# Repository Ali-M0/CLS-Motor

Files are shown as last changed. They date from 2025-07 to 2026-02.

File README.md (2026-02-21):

# CLS-Motor: A compact solution for stepper motors
<br>
<br>

Screenshot 2025-07-10 at 8 18 01 PM

<br>
<br>

          

<br>
Why not improve the capabilities of an already abundant and capable motor.
<br>

## Key Features

<br>
- Real-time closed-loop correction using MT6816 magnetic encoder
<br>
- **Communication via CAN bus:** By utilizing a CAN bus communication protocol, you inherently gain several benefits to your system, the main benefits being a robust communication protocol that was made with low EMI in mind, along with a more accurate system that decreases the amount of wires needed and scalability with other CLS-Motor systems.
<br>
- **6-layer custom PCB:** Designed in KiCad for signal integrity and thermal performance
<br>
- **Onboard STM32F103CBT6:** Handles encoder data and CAN communication
<br>
- Power regulation via LP2992AIM5-3.3 linear regulator
<br>
- Fully custom C++ to come (CLion environment)

<br>
<br>

## Motivation
In robotic systems—especially robotic arms—accuracy and reliability are critical. While working on my own robotic arm project, I noticed that traditional open-loop stepper motors often missed steps under load, compromising precision.
<br>
<br>
To solve this, I developed the Closed-Loop Stepper (CLS) Motor system—an integrated hardware/software solution that enables real-time position correction through encoder feedback and control logic.
<br>
<br>
<br>

FUTURE PLANS
<br>

># Correction Software for CLS Motor
>
><br>
><br>
>
> Explanation about my STM32 programming coming soon with demo and visuals.
> <br>
> Implementation of a diagnostic serial output to aid in tuning and debugging the control loop in real-world conditions.
> <br>
> Custom C++ software using a PID control system and FOC controller to detect missing steps, sending signals to then correct the lost steps
> <br>
>

<br>
<br>
<br>
<br>

## Technical Specifications/Overview

<br>

A closed-loop control system designed to stack with stepper motors and provide real-time feedback using a magnetic encoder. It detects missed steps and corrects them using an onboard STM32 microcontroller while also supplying your communication line through the CAN bus ports to your main microcontroller.

  <br>

In the field of robotics, precision and reliability in motor control are essential. During the development of my robotic arm project, I identified the limitations of traditional open-loop stepper systems, particularly their inability to self-correct under load. To address this, I designed and implemented a closed-loop stepper motor driver, combining custom hardware and software to enable real-time position correction.

  <br>

This project involved designing a 6-layer PCB in KiCad, optimized for signal integrity and thermal performance. At its core is an STM32F103CBT6 microcontroller, chosen for its surprisingly high processing speed, rich I/O capabilities, and the fact that its only main purpose is to power the encoder and CAN transceiver, along with any other I/O necessary within the board. I integrated an MT6816 magnetic rotary encoder on the rear shaft of a NEMA 17 stepper motor to provide high-resolution feedback, enabling the system to compare target and actual positions. Through custom correction software written in C++ using CLion, the CLS system adjusts its actuation based on the previous and current step resolution. The CLS motor system also integrates an SN65HVD232 CAN transceiver that, on the surface, enables communication between the main CAN controller located on the main MCU, that being a Teensy 4.1, and the CAN bus ports, supplying my system with its communication signal.

  <br>

You also may be wondering how my system is powered. That's done through a cascade power system that cascades through a daisy chain design and supplies power to all motors using the CLS motor system, being ultimately powered by a +5V power supply that's soldered to the PCB's positive and negative solder pads added to the top and bottom of the board. The system regulates the +5V power supply to a +3.3V output rail through an LP2992AIM5-3.3 linear regulator, and this then provides power to all the necessary components within my system.

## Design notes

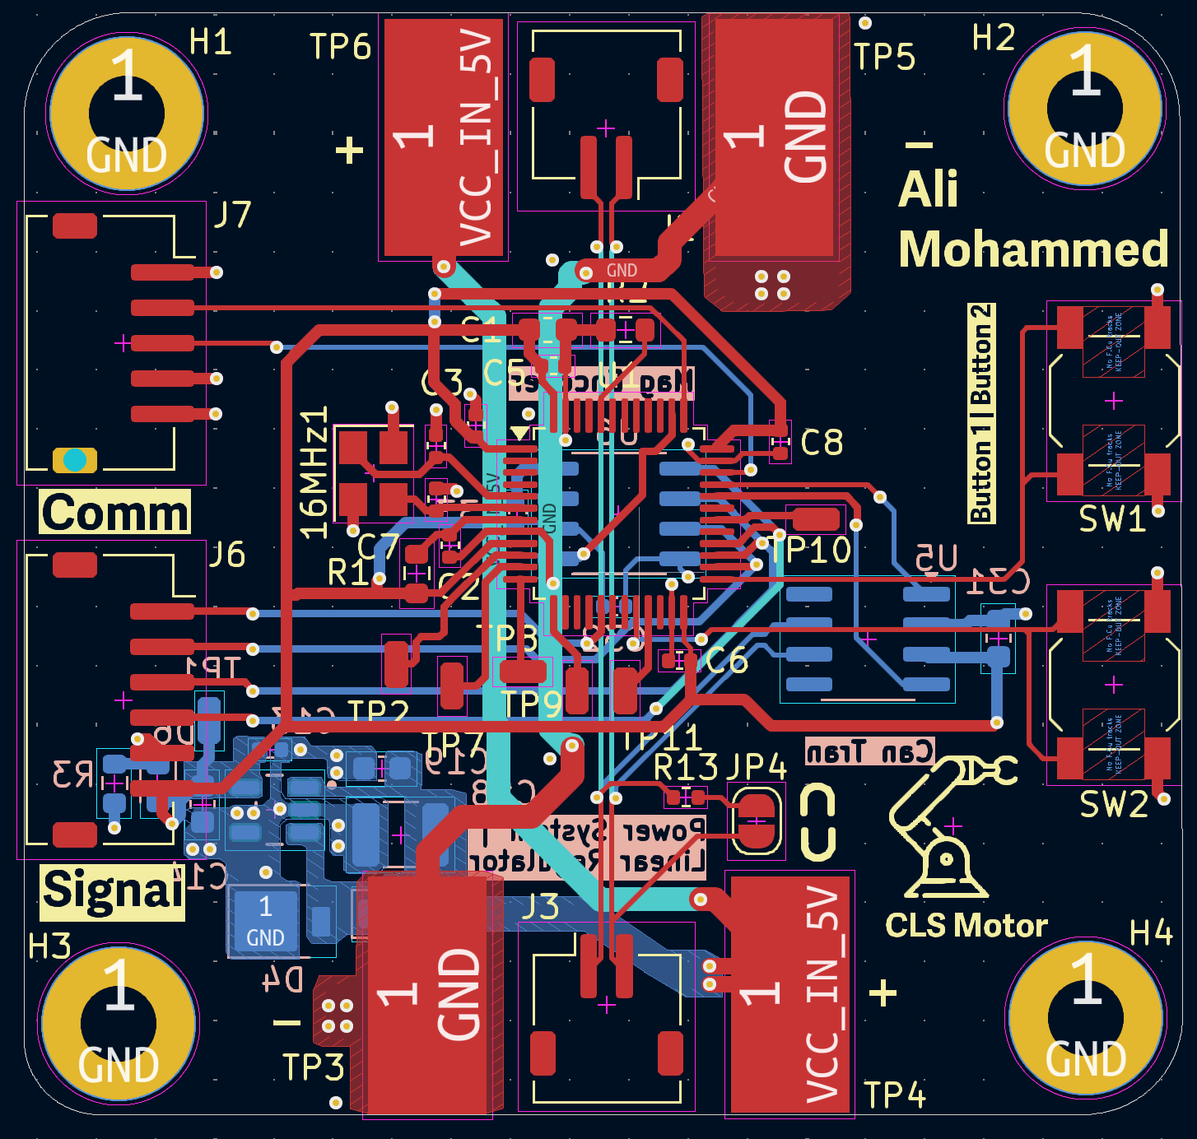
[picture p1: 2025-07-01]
Images/PCB Design in Software.png

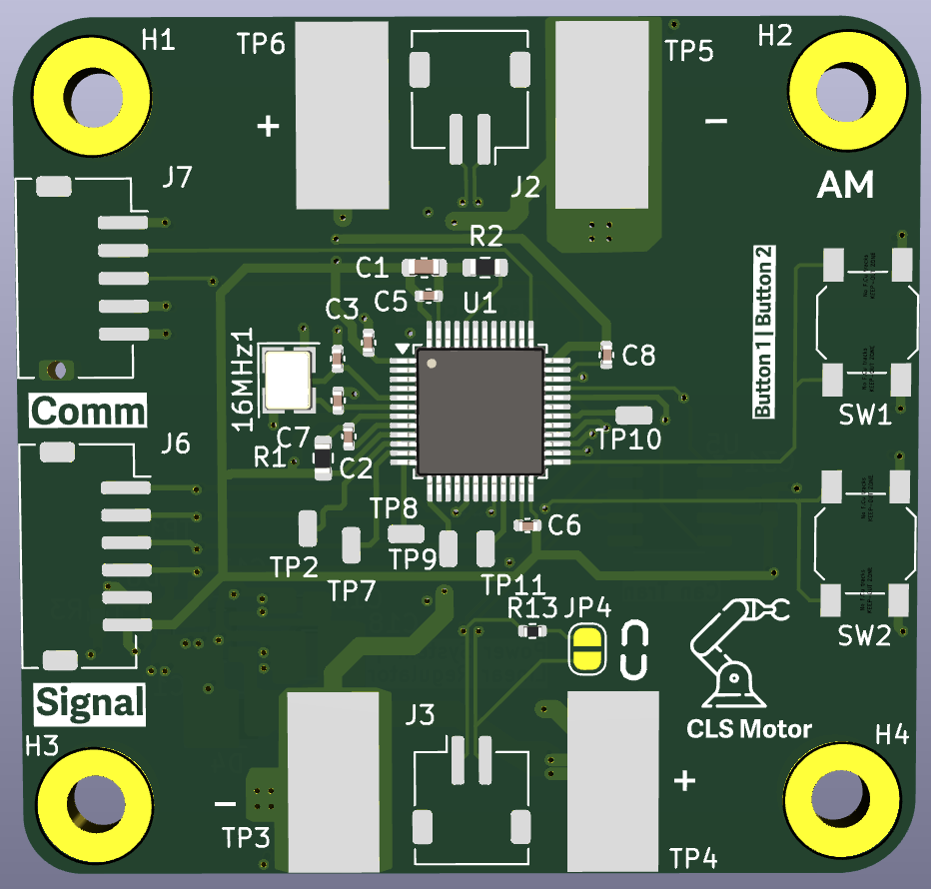
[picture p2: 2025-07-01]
Images/PCB Render (Front).png

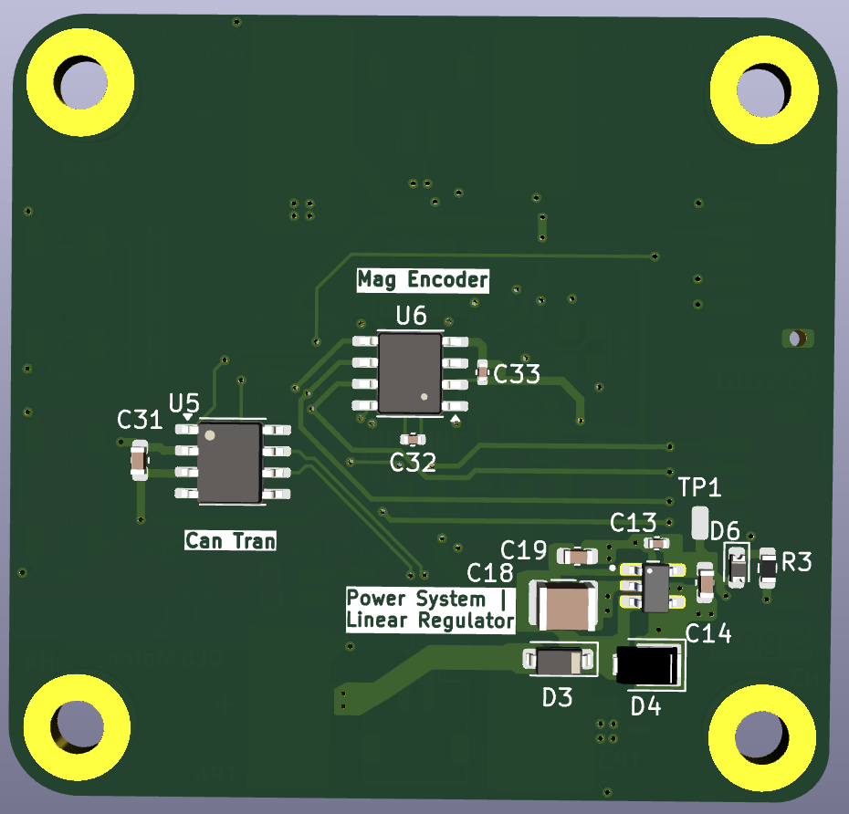
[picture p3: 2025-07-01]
Images/PCB Render (Back).png

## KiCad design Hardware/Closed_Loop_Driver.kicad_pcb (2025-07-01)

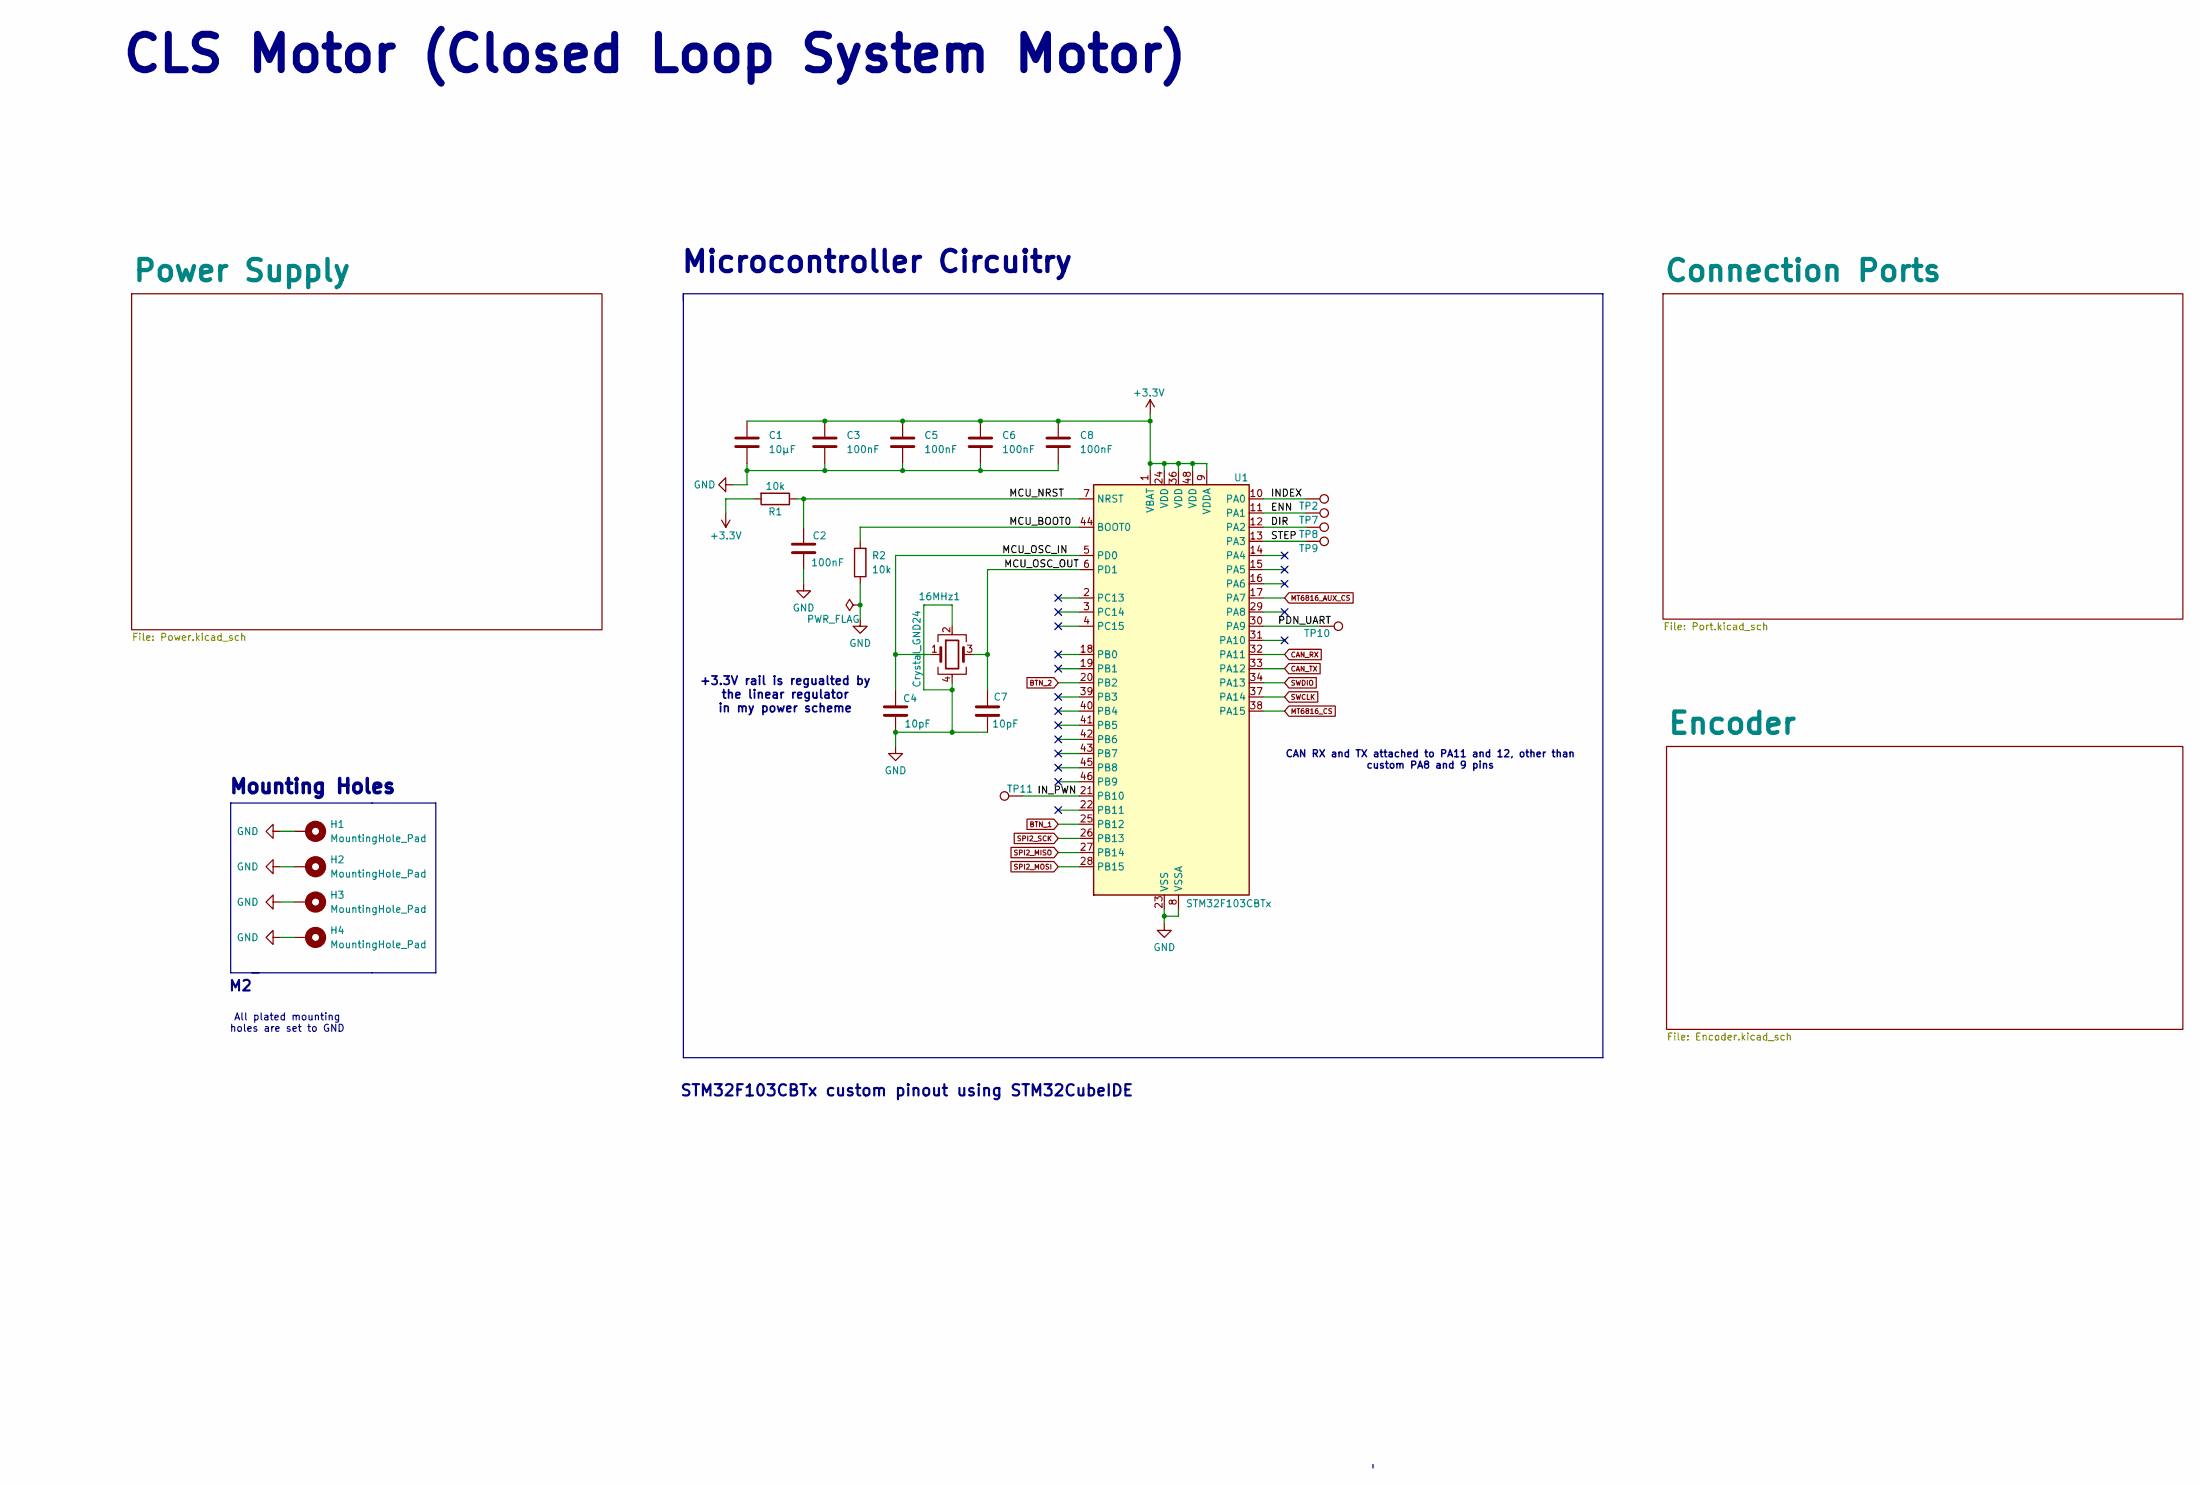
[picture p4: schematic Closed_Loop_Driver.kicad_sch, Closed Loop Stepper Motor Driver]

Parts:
16MHz1: Crystal_GND24; Crystal_SMD_3225-4Pin_3.2x2.5mm
C1: 10µF; C_0603_1608Metric
C2, C3, C5, C6, C8: 100nF; C_0402_1005Metric
C4, C7: 10pF; C_0402_1005Metric
H1, H2, H3, H4: MountingHole_Pad; MountingHole_3.2mm_M3_Pad
R1, R2: 10k; R_0603_1608Metric
TP2, TP7, TP8, TP9, TP10, TP11: TestPoint; SolderWirePad_1x01_SMD_1x2mm
U1: STM32F103CBTx; LQFP-48_7x7mm_P0.5mm

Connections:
+3.3V: C1.1, C3.1, C5.1, C6.1, C8.1, R1.2, U1.1 (VBAT), U1.9 (VDDA), U1.24 (VDD), U1.36 (VDD), U1.48 (VDD); also elsewhere on the board
/DIR: TP8.1, U1.12 (PA2)
/ENN: TP7.1, U1.11 (PA1)
/INDEX: TP2.1, U1.10 (PA0)
/IN_PWN: TP11.1, U1.21 (PB10)
/MCU_BOOT0: R2.2, U1.44 (BOOT0)
/MCU_NRST: C2.1, R1.1, U1.7 (NRST)
/MCU_OSC_IN: 16MHz1.1, C4.1, U1.5 (PD0)
/MCU_OSC_OUT: 16MHz1.3, C7.1, U1.6 (PD1)
/PDN_UART: TP10.1, U1.30 (PA9)
/STEP: TP9.1, U1.13 (PA3)
BTN_1: U1.25 (PB12); also elsewhere on the board
BTN_2: U1.20 (PB2); also elsewhere on the board
CAN_RX: U1.32 (PA11); also elsewhere on the board
CAN_TX: U1.33 (PA12); also elsewhere on the board
GND: 16MHz1.2, 16MHz1.4, C1.2, C2.2, C3.2, C4.2, C5.2, C6.2, C7.2, C8.2, H1.1, H2.1, H3.1, H4.1, R2.1, U1.8 (VSSA), U1.23 (VSS), U1.35 (VSS), U1.47 (VSS); also elsewhere on the board
MT6816_AUX_CS: U1.17 (PA7); also elsewhere on the board
MT6816_CS: U1.38 (PA15); also elsewhere on the board
SPI2_MISO: U1.27 (PB14); also elsewhere on the board
SPI2_MOSI: U1.28 (PB15); also elsewhere on the board
SPI2_SCK: U1.26 (PB13); also elsewhere on the board
SWCLK: U1.37 (PA14); also elsewhere on the board
SWDIO: U1.34 (PA13); also elsewhere on the board

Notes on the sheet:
CLS Motor (Closed Loop System Motor)
CAN RX and TX attached to PA11 and 12, other than custom PA8 and 9 pins
All plated mounting holes are set to GND
Microcontroller Circuitry
+3.3V rail is regualted by the linear regulator in my power scheme
Mounting Holes
STM32F103CBTx custom pinout using STM32CubeIDE

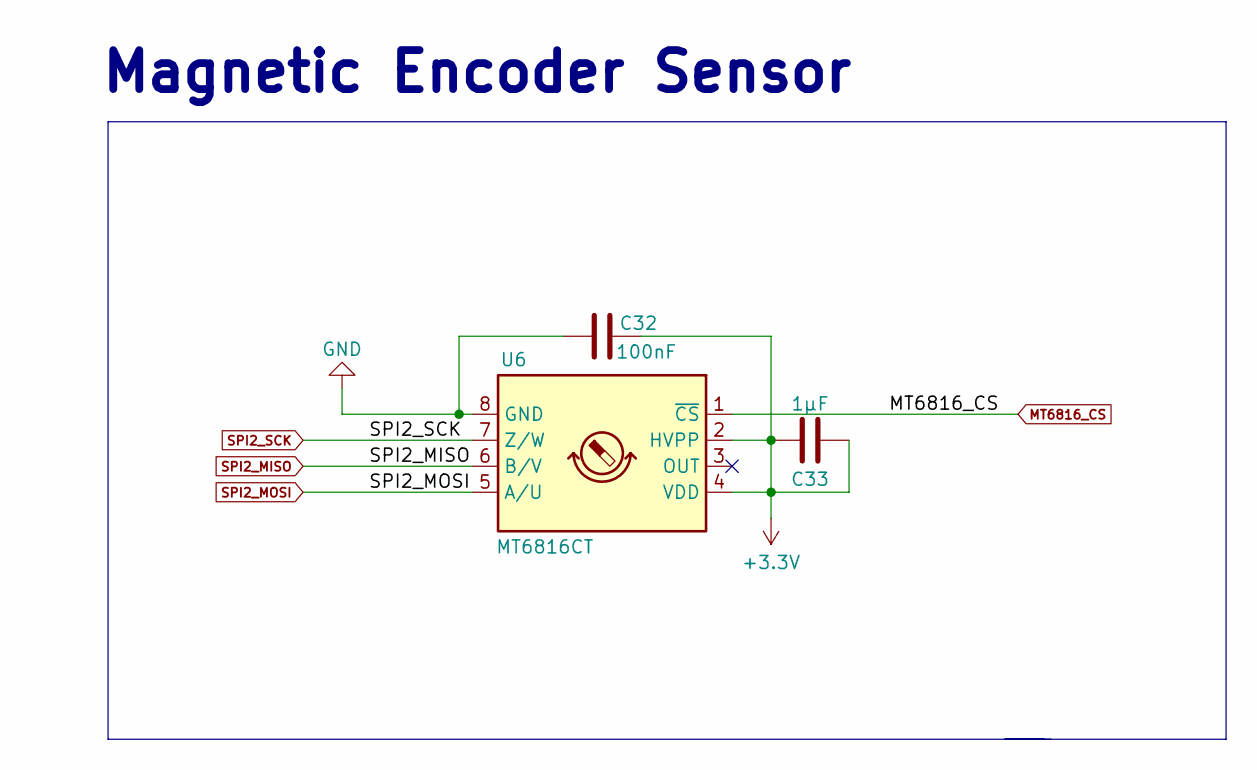
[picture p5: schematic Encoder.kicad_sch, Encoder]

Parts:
C32: 100nF; C_0402_1005Metric
C33: 1µF; C_0402_1005Metric
U6: MT6816CT; SO-8_3.9x4.9mm_P1.27mm

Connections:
+3.3V: C32.1, C33.1, C33.2, U6.2 (HVPP), U6.4 (VDD); also elsewhere on the board
GND: C32.2, U6.8 (GND); also elsewhere on the board
MT6816_CS: U6.1 (~CS); also elsewhere on the board
SPI2_MISO: U6.6 (B/V); also elsewhere on the board
SPI2_MOSI: U6.5 (A/U); also elsewhere on the board
SPI2_SCK: U6.7 (Z/W); also elsewhere on the board

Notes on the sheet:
Magnetic Encoder Sensor

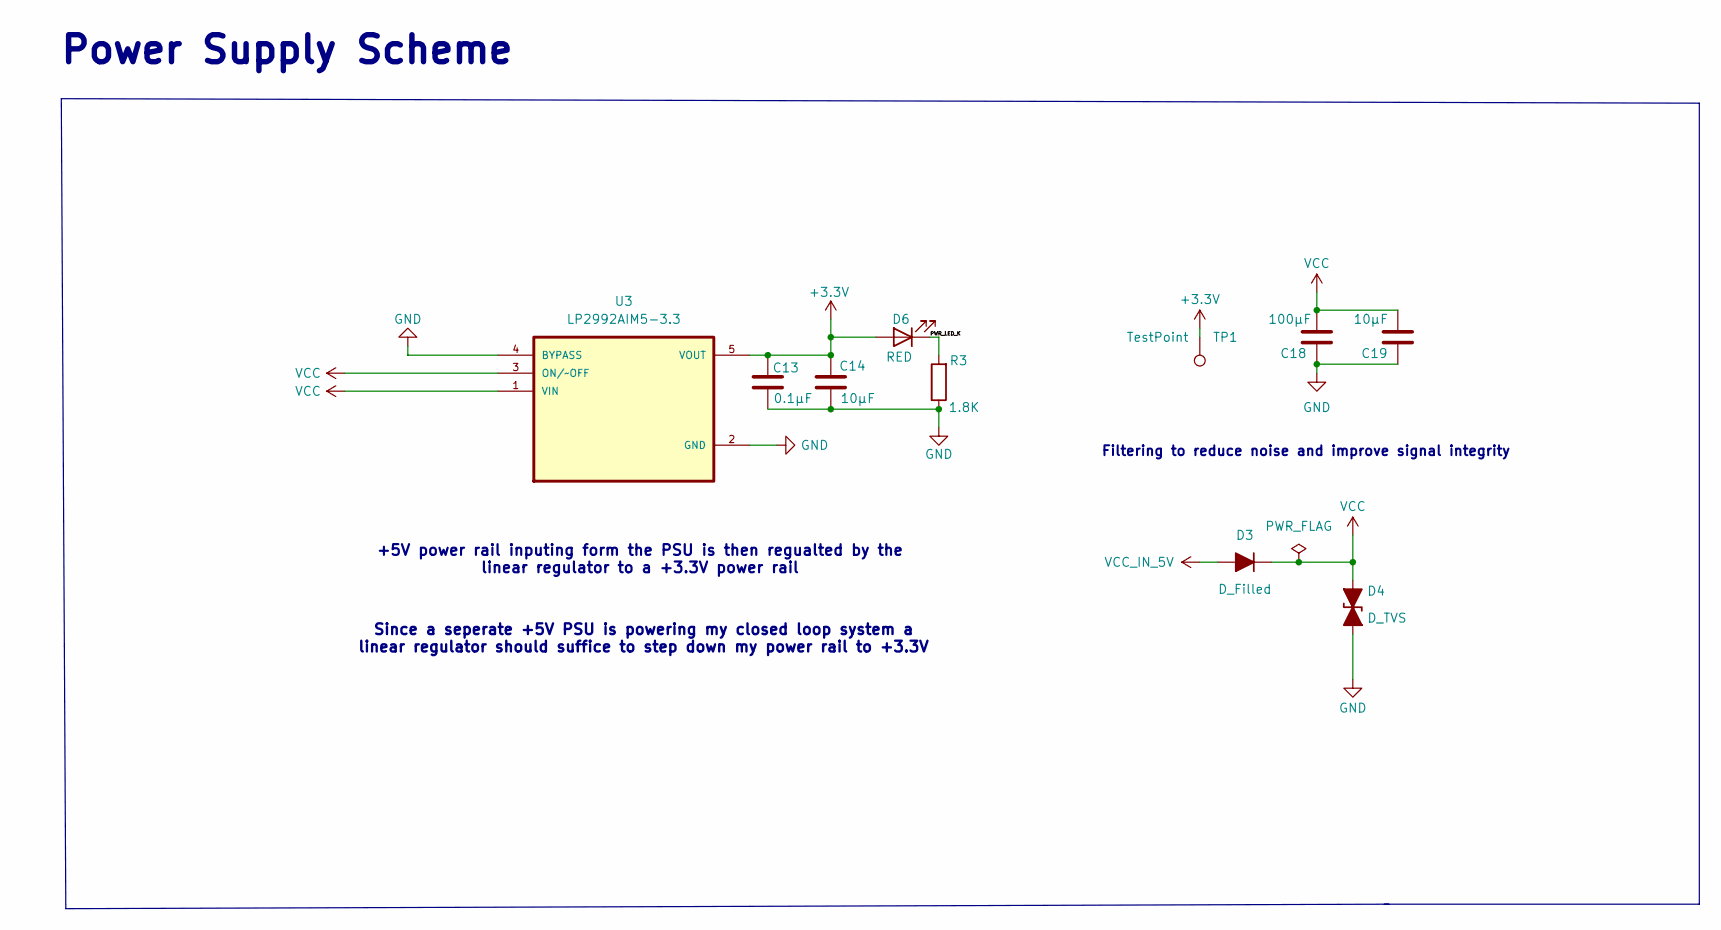
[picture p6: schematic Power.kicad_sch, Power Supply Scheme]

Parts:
C13: 0.1µF; C_0402_1005Metric
C14, C19: 10µF; C_0603_1608Metric
C18: 100µF; C_1210_3225Metric
D3: D_Filled; D_SOD-123
D4: D_TVS; D_SMP_DO-220AA
D6: RED; D_0603_1608Metric
R3: 1.8K; R_0603_1608Metric
TP1: TestPoint; SolderWirePad_1x01_SMD_1x2mm
U3: LP2992AIM5-3.3; SOT95P280X145-5N

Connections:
+3.3V: C13.1, C14.2, D6.2 (A), TP1.1, U3.5 (VOUT); also elsewhere on the board
/Power Supply/PWR_LED_K: D6.1 (K), R3.2
GND: C13.2, C14.1, C18.2, C19.2, D4.1 (A1), R3.1, U3.2 (GND), U3.4 (BYPASS); also elsewhere on the board
VCC: C18.1, C19.1, D3.1 (K), D4.2 (A2), U3.1 (VIN), U3.3 (ON/~OFF)
VCC_IN_5V: D3.2 (A); also elsewhere on the board

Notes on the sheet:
+5V power rail inputing form the PSU is then regualted by the linear regulator to a +3.3V power rail
Power Supply Scheme
Since a seperate +5V PSU is powering my closed loop system a linear regulator should suffice to step down my power rail to +3.3V
Filtering to reduce noise and improve signal integrity

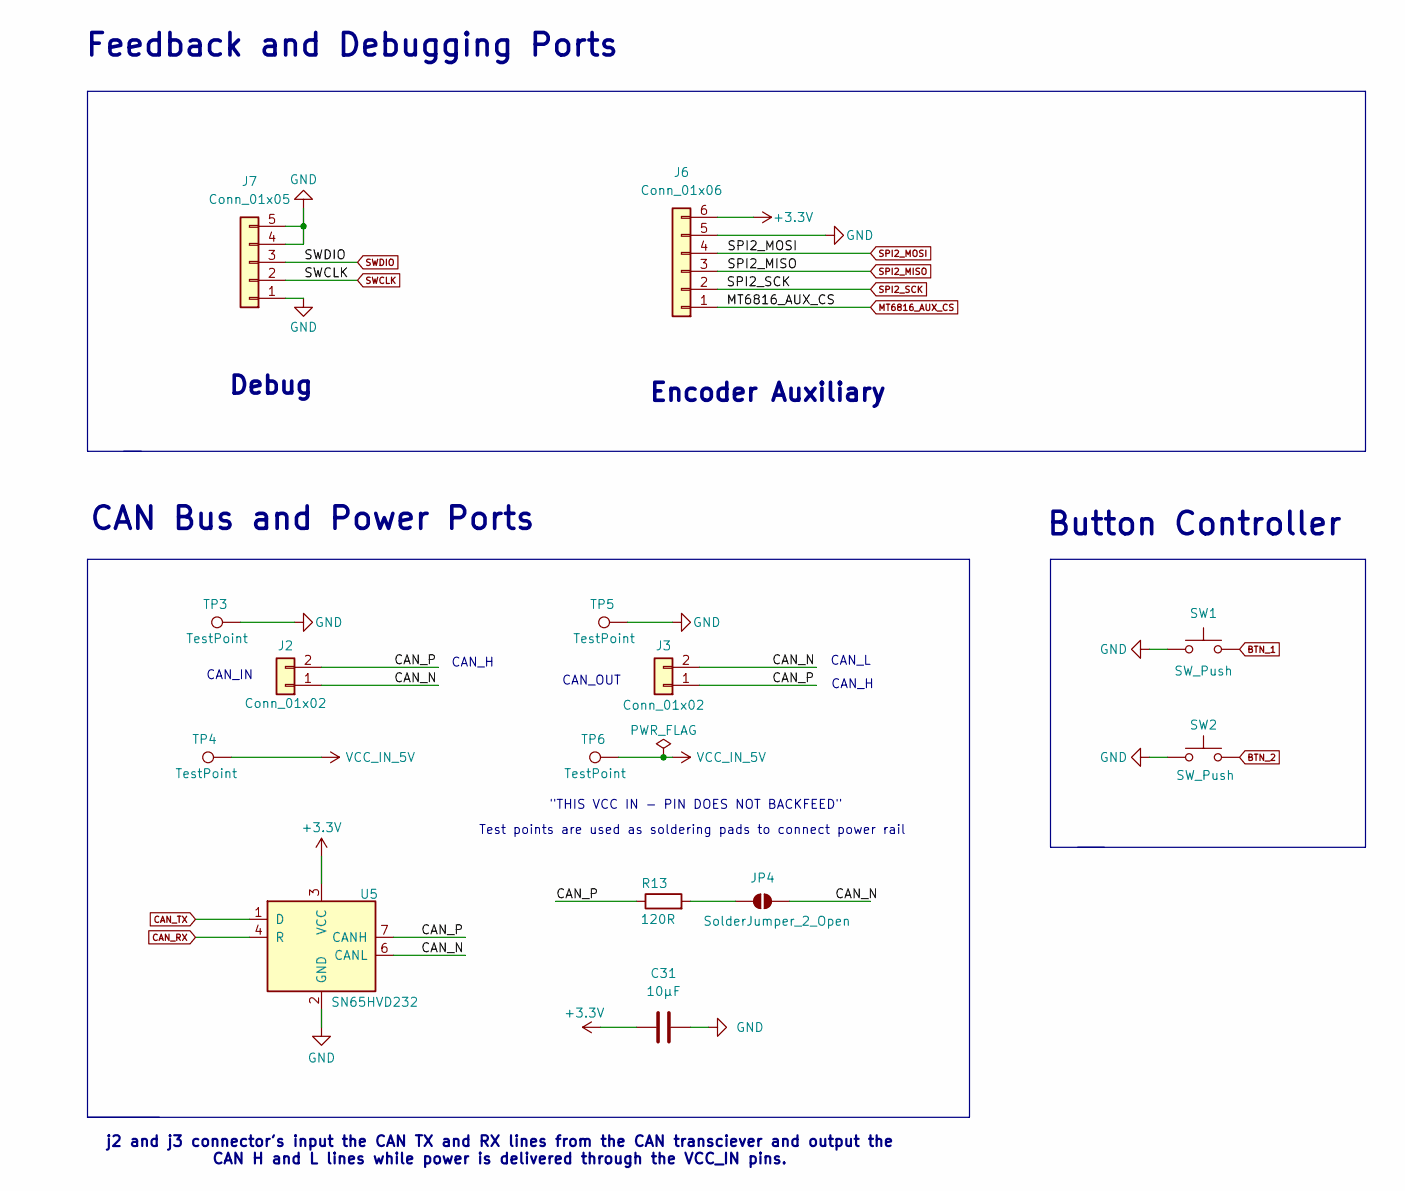
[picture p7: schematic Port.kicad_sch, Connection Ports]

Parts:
C31: 10µF; C_0603_1608Metric
J2, J3: Conn_01x02; JST_ZH_S2B-ZR-SM4A-TF_1x02-1MP_P1.50mm_Horizontal
J6: Conn_01x06; JST_ZH_S6B-ZR-SM4A-TF_1x06-1MP_P1.50mm_Horizontal
J7: Conn_01x05; JST_ZH_S5B-ZR-SM4A-TF_1x05-1MP_P1.50mm_Horizontal
JP4: SolderJumper_2_Open; SolderJumper-2_P1.3mm_Open_RoundedPad1.0x1.5mm
R13: 120R; R_0402_1005Metric
SW1, SW2: SW_Push; SW_SPST_SKQG_WithStem
TP3, TP4, TP5, TP6: TestPoint; SolderWirePad_1x01_SMD_5x10mm
U5: SN65HVD232; SOIC-8_3.9x4.9mm_P1.27mm

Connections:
+3.3V: C31.1, J6.6, U5.3 (VCC); also elsewhere on the board
/Connection Ports/CAN_N: J2.1, J3.2, JP4.2 (B), U5.6 (CANL)
/Connection Ports/CAN_P: J2.2, J3.1, R13.1, U5.7 (CANH)
BTN_1: SW1.2; also elsewhere on the board
BTN_2: SW2.2; also elsewhere on the board
CAN_RX: U5.4 (R); also elsewhere on the board
CAN_TX: U5.1 (D); also elsewhere on the board
GND: C31.2, J6.5, J7.1, J7.4, J7.5, SW1.1, SW2.1, TP3.1, TP5.1, U5.2 (GND); also elsewhere on the board
MT6816_AUX_CS: J6.1; also elsewhere on the board
unnamed: JP4.1 (A), R13.2
SPI2_MISO: J6.3; also elsewhere on the board
SPI2_MOSI: J6.4; also elsewhere on the board
SPI2_SCK: J6.2; also elsewhere on the board
SWCLK: J7.2; also elsewhere on the board
SWDIO: J7.3; also elsewhere on the board
VCC_IN_5V: TP4.1, TP6.1; also elsewhere on the board

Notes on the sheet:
CAN_L
CAN Bus and Power Ports
CAN_IN
CAN_H
Button Controller
Feedback and Debugging Ports
"THIS VCC IN - PIN DOES NOT BACKFEED"
Test points are used as soldering pads to connect power rail
j2 and j3 connector's input the CAN TX and RX lines from the CAN transciever and output the CAN H and L lines while power is delivered through the VCC_IN pins.
Encoder Auxiliary
CAN_OUT
Debug

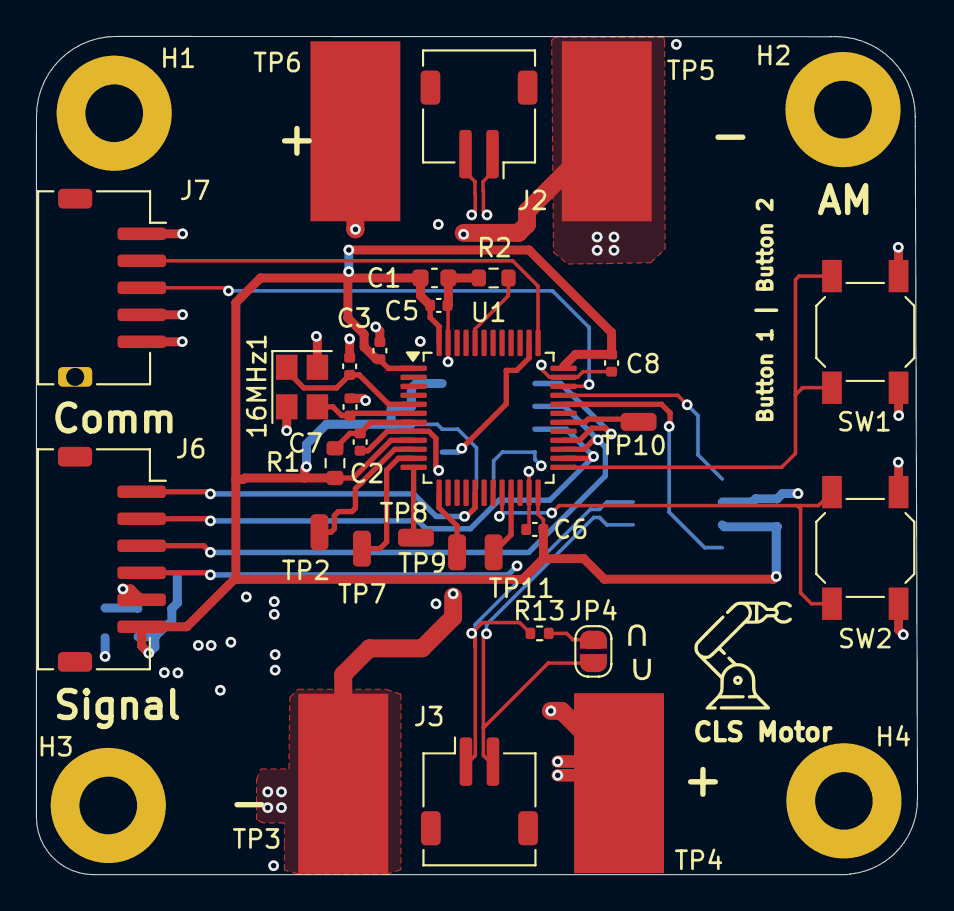
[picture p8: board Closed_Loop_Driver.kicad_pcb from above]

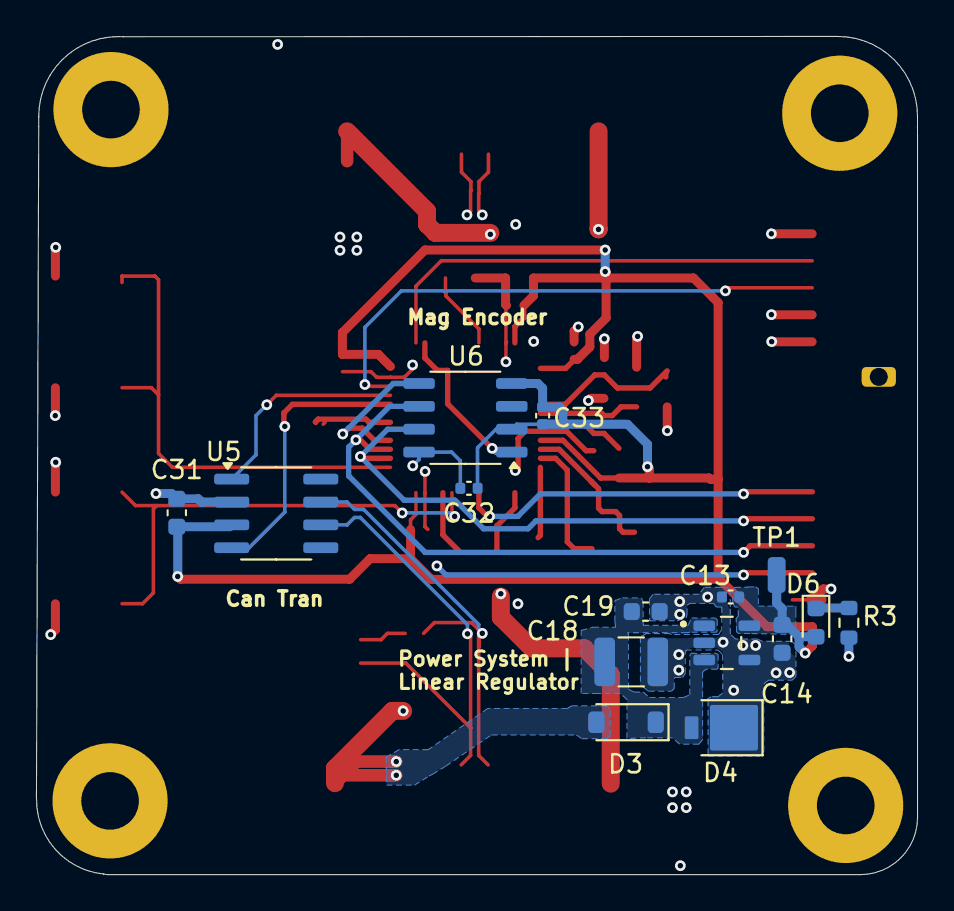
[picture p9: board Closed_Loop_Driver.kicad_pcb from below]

Board: 6 copper layers, 48.9 x 46.6 mm, 49 parts (15 on the bottom side), 29 nets.

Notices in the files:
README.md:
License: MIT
